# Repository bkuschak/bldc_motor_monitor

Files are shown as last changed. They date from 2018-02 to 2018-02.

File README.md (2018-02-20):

# bldc_motor_monitor
This is a tachometer, counter, and current meter for the LMS 5200 mini-lathe, LMS 3990 mini-mill and similar tools that use the XMT-DRV-500C(3) / ZM3404 BLDC motor controller.

This project provides a small 2x16 line LCD display showing:
- Spindle RPM and direction
- Spindle revolution counter
- Motor current

It consists of a small PCB hosting the LCD, Arduino Micro R3, and connectors that mate inline with the BLDC sensor cable. It uses an 
optional toroidal transformer to sense AC line current.  A single pushbutton is used to clear the rev count and alternate between
modes.

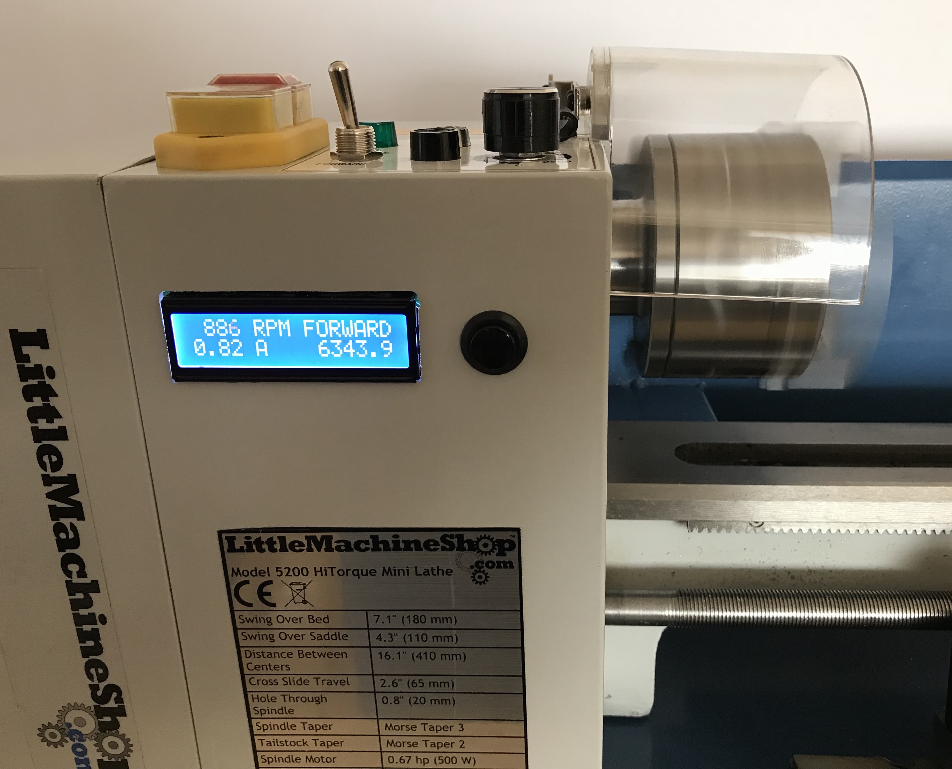
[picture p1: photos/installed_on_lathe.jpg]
Installed


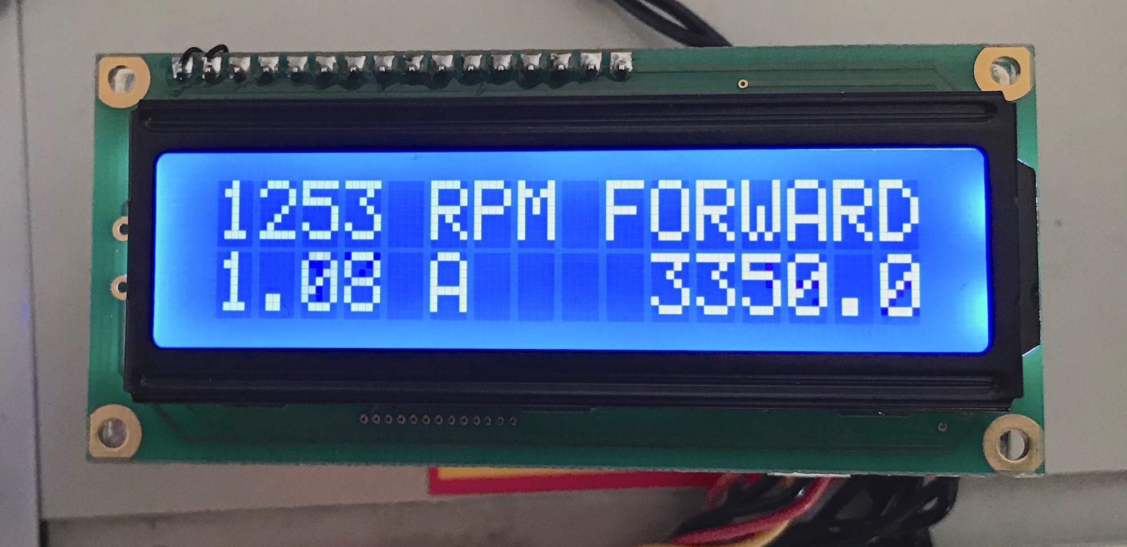
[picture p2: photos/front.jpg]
Front


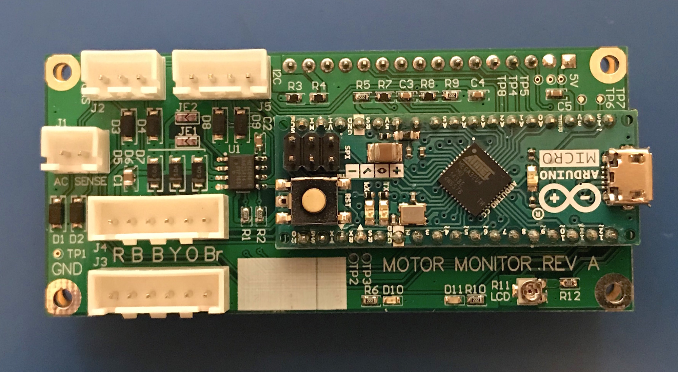
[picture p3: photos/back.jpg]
Back


This project was motivated by the need to keep an accurate count of spindle revolutions while winding coils on a mini-lathe. 
Since the BLDC motor controller already has a means of tracking spindle revolutions, it was easy to tap into this circuit rather than 
adding external encoders or hall-effect sensors.  

The motor controller in my lathe is this one pictured below. I haven't been able to find much good documentation on this board,
but it does seem to be pretty widely used. The pinout for the hall-effect connector is learned by inspection.  Recently I found 
a [very low-quality schematic](doc/500W-1000W_spindle_control_PCB_01.jpg?raw=true). It may or may not be for this particular driver board. 

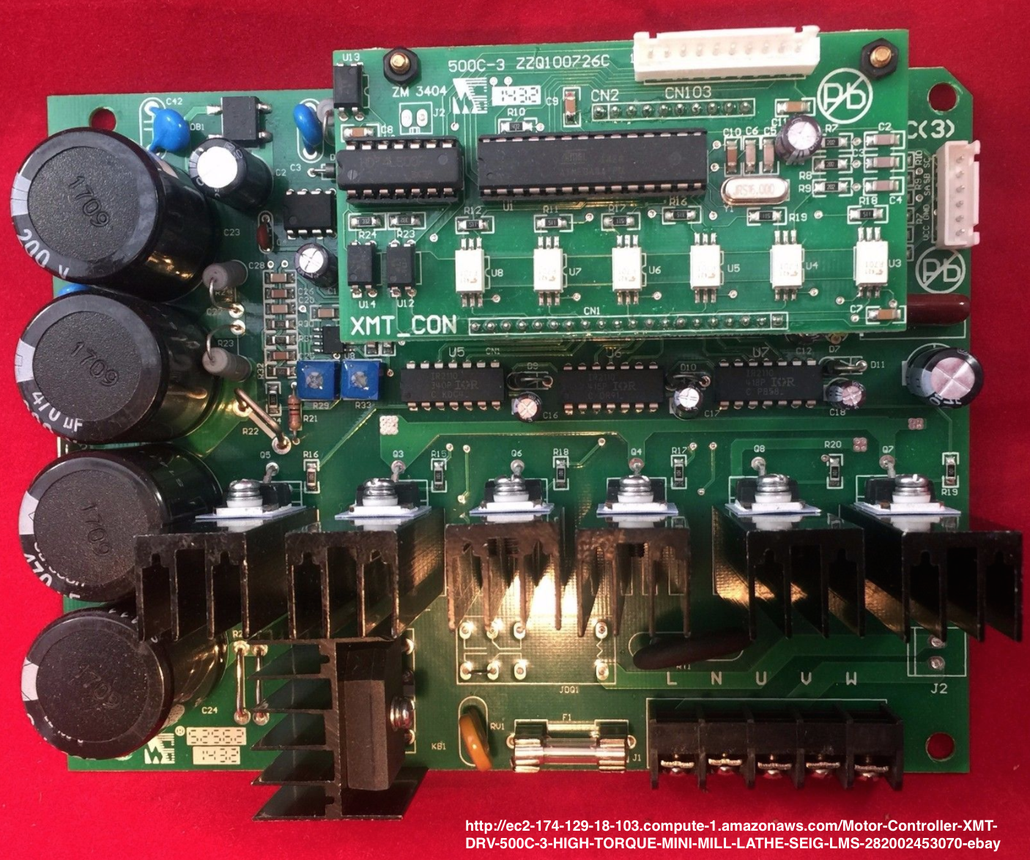
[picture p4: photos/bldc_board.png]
BLDC Board


### WARNING and DISCLAIMER
Although the BLDC 5V power seems to be isolated from AC mains and chassis, be careful to avoid 
risk of shock. I have no control over your BLDC driver circuitry, and it might zap you if you touch it. 
It is possible your machine uses a different driver board or a different hardware revision that is incompatible, even if it looks similar.
**Using this project can result in damage to your equipment, and danger or injury to yourself. If you choose to use 
this project, I will not be held liable for any damage or injury or repairs.**  Take all the usual precautions when working 
with AC-mains powered equipment. To avoid risk of damage to your PC, do not connect to the Arduino USB while the board is connected 
to the motor controller.

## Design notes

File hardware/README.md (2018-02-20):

## hardware

The schematics and PCB were created in Altium 16.

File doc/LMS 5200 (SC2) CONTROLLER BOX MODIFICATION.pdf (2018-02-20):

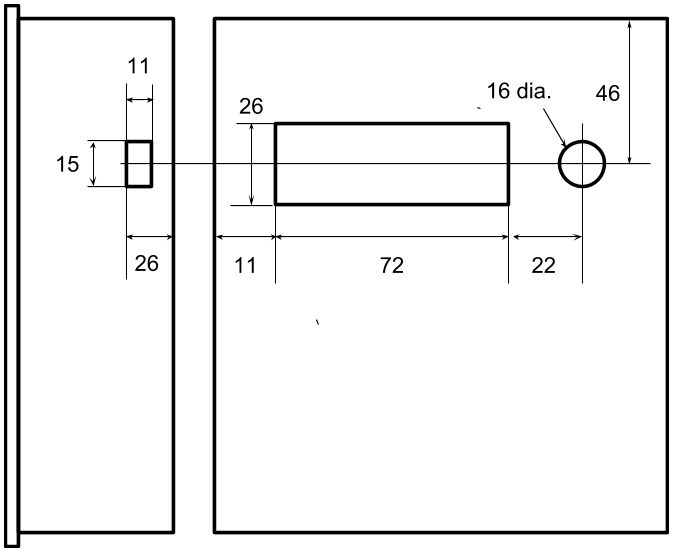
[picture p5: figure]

Dimensions in mm

LMS 5200 (SC2) CONTROLLER BOX MODIFICATION

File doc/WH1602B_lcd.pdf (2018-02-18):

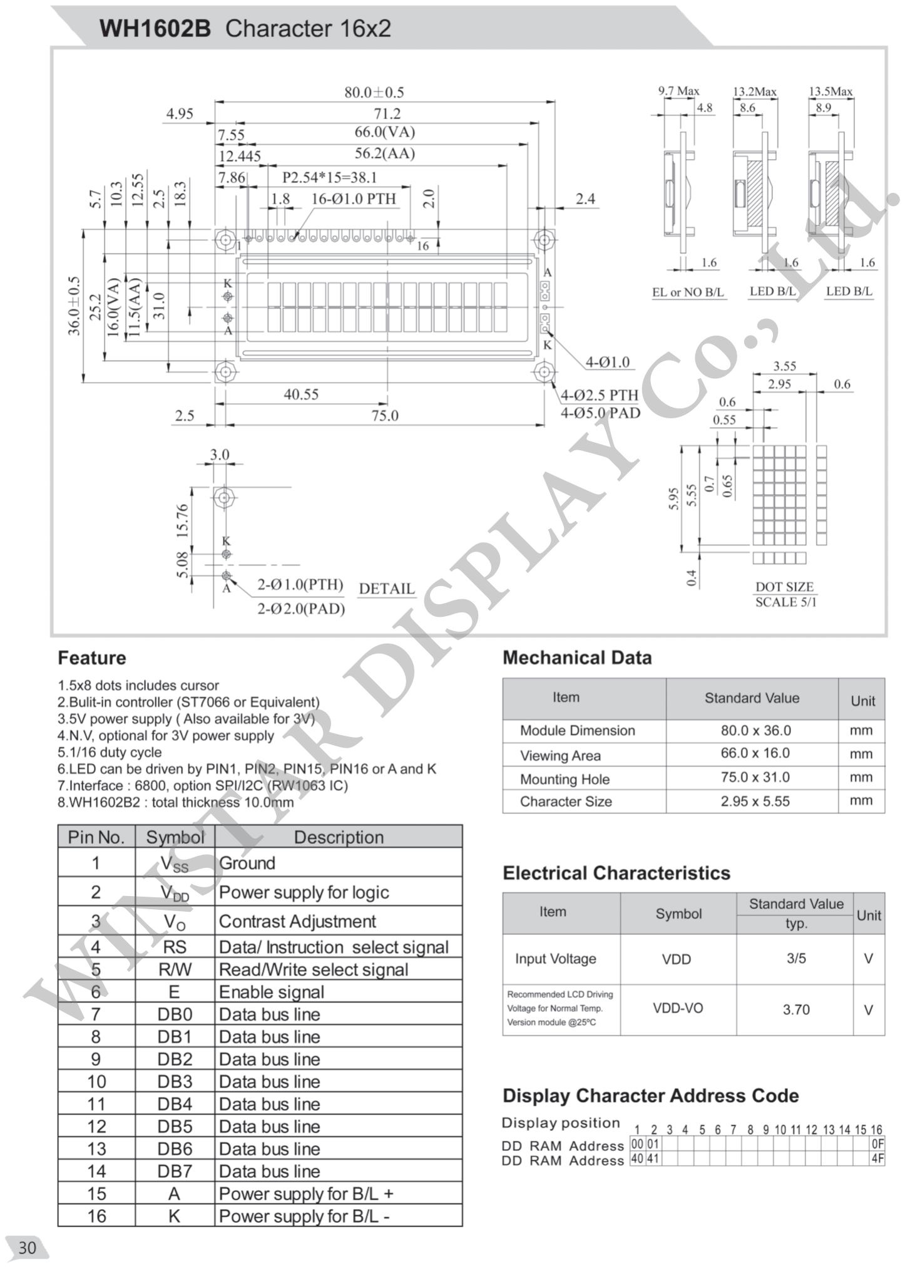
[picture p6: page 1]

WINSTAR DISPLAY Co., Ltd.

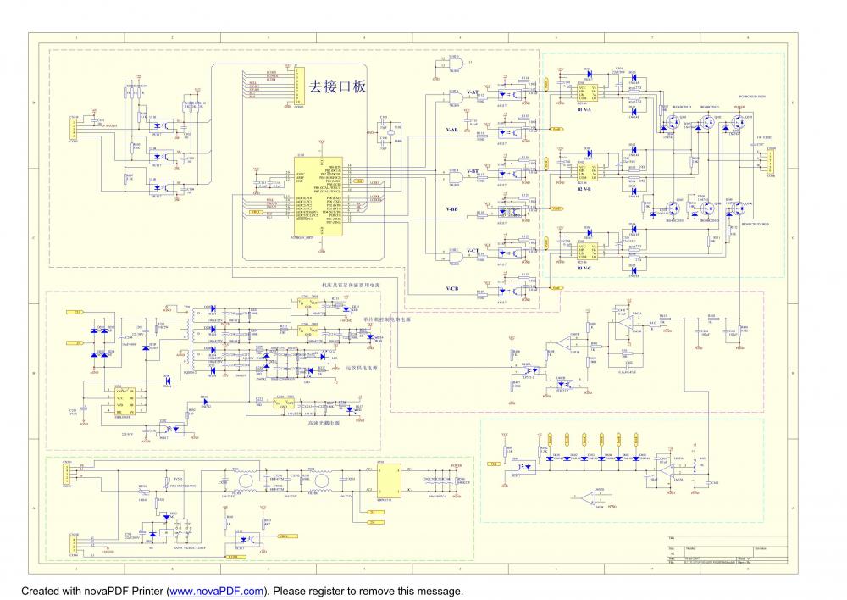
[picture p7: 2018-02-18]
doc/500W-1000W_spindle_control_PCB_01.jpg

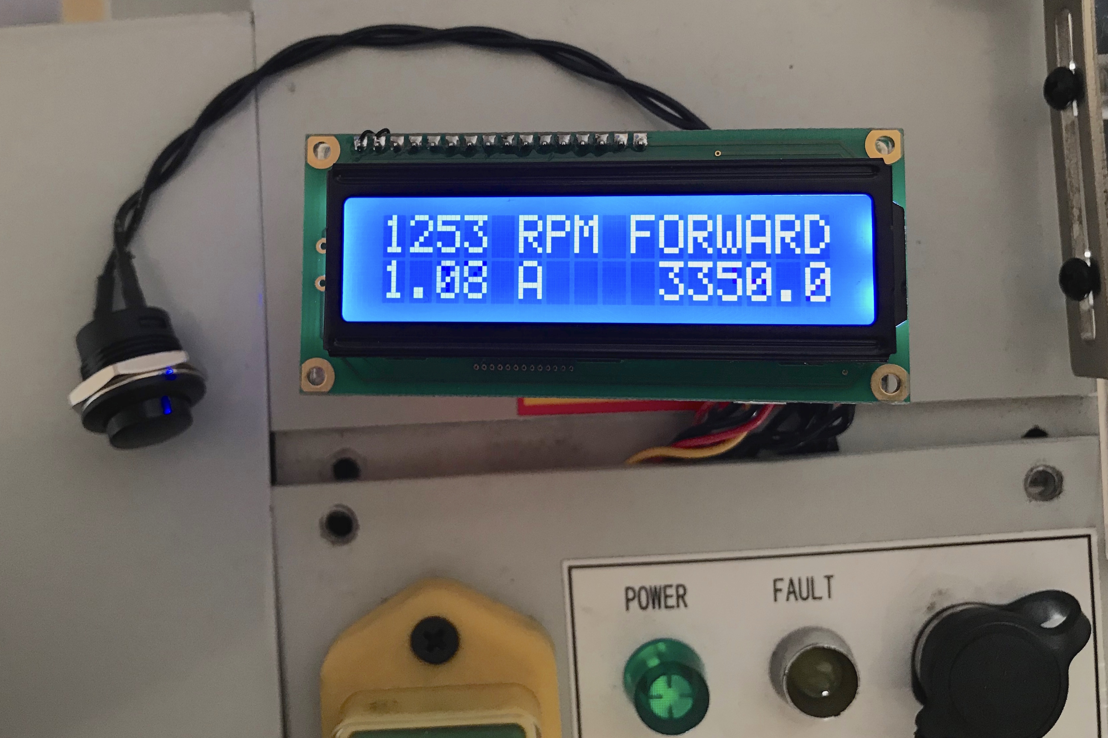
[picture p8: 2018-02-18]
photos/motor_monitor_pcb.jpg

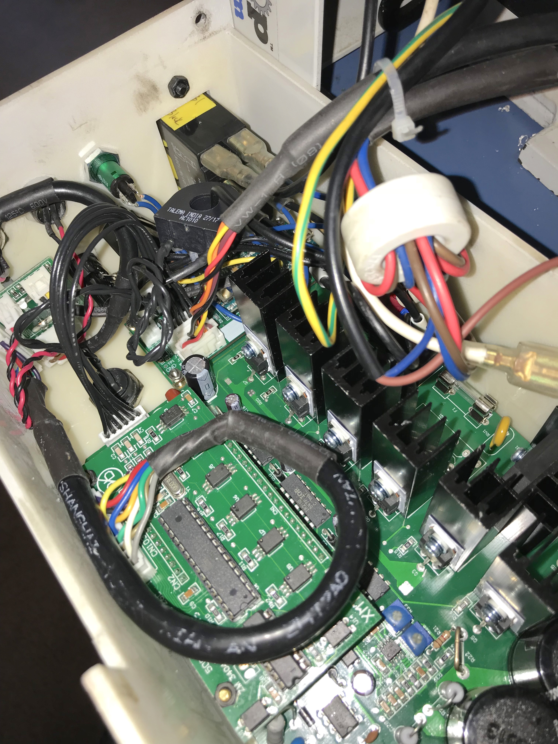
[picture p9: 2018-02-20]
photos/motor_controller_box_lathe2.jpg

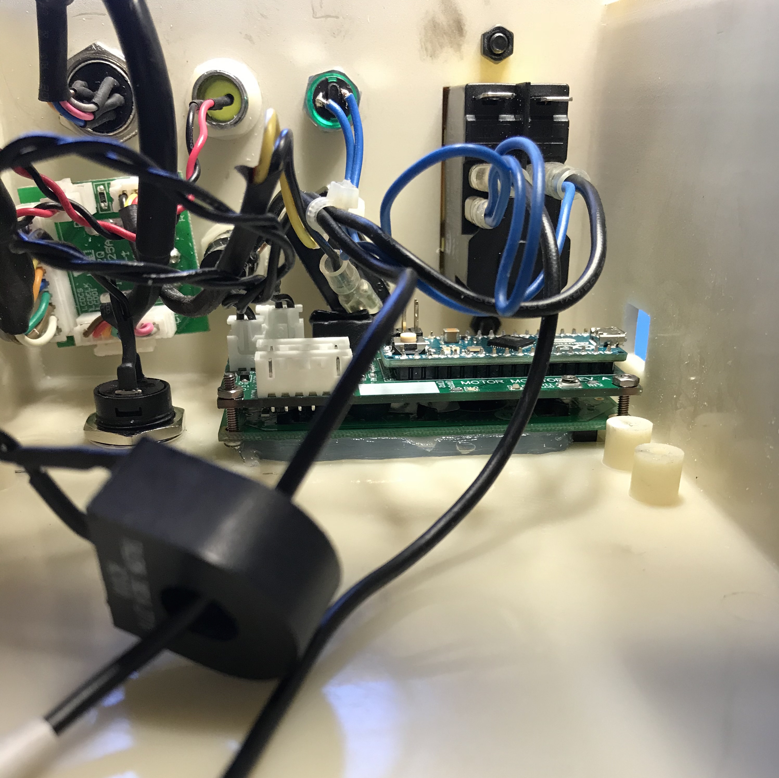
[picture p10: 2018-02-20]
photos/motor_controller_box_lathe1.jpg

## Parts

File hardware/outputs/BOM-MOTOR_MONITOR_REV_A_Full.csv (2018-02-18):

Quantity | DNS | Designator | Description | Footprint | Manufacturer | PartNumber | Digikey | Notes
1 |  | C1 | CAP CER 10UF 10V X7R 0805 | CAP 0805/2012 | Murata Electronics North America | GRM21BR71A106KE51L
4 |  | C2, C3, C4, C5 | CAP CER 0.1UF 16V X7R 0603 | CAP 0603/1608 | Murata Electronics North America | GRM188R71C104KA01D
9 |  | D1, D2, D3, D4, D5, D6, D7, D8, D9 | TVS DIODE 5VWM 9.2VC SOD123 | SOD123F | Littelfuse Inc. | SMF5.0A
1 |  | D10 | Typical RED, GREEN, YELLOW, AMBER GaAs LED | 0603R-GENERIC | Lite-On | LTST-C194KGKT
1 |  | D11 | Typical RED, GREEN, YELLOW, AMBER GaAs LED | 0603R-GENERIC | Osram | LS Q976-NR-1
1 |  | J1 | CONN HEADER XH TOP 2POS 2.5MM | JST XH B2B-XH-A | JST Sales America Inc. | B2B-XH-A(LF)(SN)
1 |  | J2 | CONN HEADER XH TOP 3POS 2.5MM | JST XH B3B-XH-A | JST Sales America Inc. | B3B-XH-A(LF)(SN)
2 |  | J3, J4 | CONN HEADER XH TOP 6POS 2.5MM | JST XH B6B-XH-A | DONGGUAN XINPEI PLASTIC HARDWARE ELECTRONIC CO LTD. | A2501WVB-06P |  | Preferred connector
2 | DNS | J3, J4 | CONN HEADER XH TOP 6POS 2.5MM | JST XH B6B-XH-A | JST Sales America Inc. | B6B-XH-A(LF)(SN) |  | Non latching substitute
1 |  | J5 | CONN HEADER XH TOP 4POS 2.5MM | JST XH B4B-XH-A | JST Sales America Inc. | B4B-XH-A(LF)(SN)
7 |  | R1, R2, R5, R6, R9, R10, R12 | RES SMD 2.2K OHM 5% 1/10W 0603 | RES 0603/1608 | Panasonic Electronic Components | ERJ-3GEYJ222V
4 |  | R3, R4, R7, R8 | RES SMD 51 OHM 5% 1/4W 0603 | RES 0603/1608 | Panasonic Electronic Components | ERJ-PA3J510V
1 |  | R11 | TRIMMER 2K OHM 0.15W SMD | POT Panasonic EVM | Panasonic Electronic Components | EVM-3YSX50B23
1 |  | U1 | FM24C04B FRAM | SO8_N | Cypress | FM24C04B-G | 428-3190-ND
1 | DNS | U2 | Arduino Micro R3 | ARDUINO_MICRO_R3 | Arduino | Micro R3
1 | DNS | U3 | 2x16 LCD STN Blue Negative |  | Winstar | WH1602B-TMI-JT
External components:
12 |  |  | Tin-plated terminals |  | DONGGUAN XINPEI PLASTIC HARDWARE ELECTRONIC CO LTD. | A2501-TBE |  | Preferred connector
1 |  |  | CONN HOUSING 2.5MM XH 6POS, LATCHING |  | DONGGUAN XINPEI PLASTIC HARDWARE ELECTRONIC CO LTD. | A2501HB-06P |  | Preferred connector terminals
1 | DNS |  | CONN HOUSING 2.5MM XH 6POS |  | JST Sales America Inc. | XHP-6 | 455-2218-ND | Non-latching substitute
1 |  |  | CONN HOUSING 2.5MM XH 3POS |  | JST Sales America Inc. | XHP-3 | 455-2219-ND
1 |  |  | CONN HOUSING 2.5MM XH 2POS |  | JST Sales America Inc. | XHP-2 | 455-2266-ND
11 |  |  | Jumper wire 6 inch |  | JST Sales America Inc. | ASXHSXH22K152 | 455-3240-ND
1 |  |  | SWITCH PUSH SPST-NO 6A 125V |  | CW Industries | GPB507A05BB | SW636-ND
1 |  |  | CURR SENSE XFMR 10A T/H |  | Talema Group | AC1010 | 1295-1102-ND
3 |  |  | Rubber bumbers |  | 3M | SJ-5003 (BLACK) | SJ5003-0-ND

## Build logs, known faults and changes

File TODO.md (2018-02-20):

## TODO

Several improvements should be made on the next rev:
- Fix swapped pins 1,2 on the LCD panel.
- DNS the I2C header, since it interferes with the forward/reverse switch.
- Add a DIP switch setting for forward/reverse sense, since lathe and mill use different direction for 'forward'.
- Add an output header to provide an (open-collector?) rotation and index pulses for use with a CNC controller.
- Avoid FRAM data corruption.
- Consider alternative OLED display with faster response.

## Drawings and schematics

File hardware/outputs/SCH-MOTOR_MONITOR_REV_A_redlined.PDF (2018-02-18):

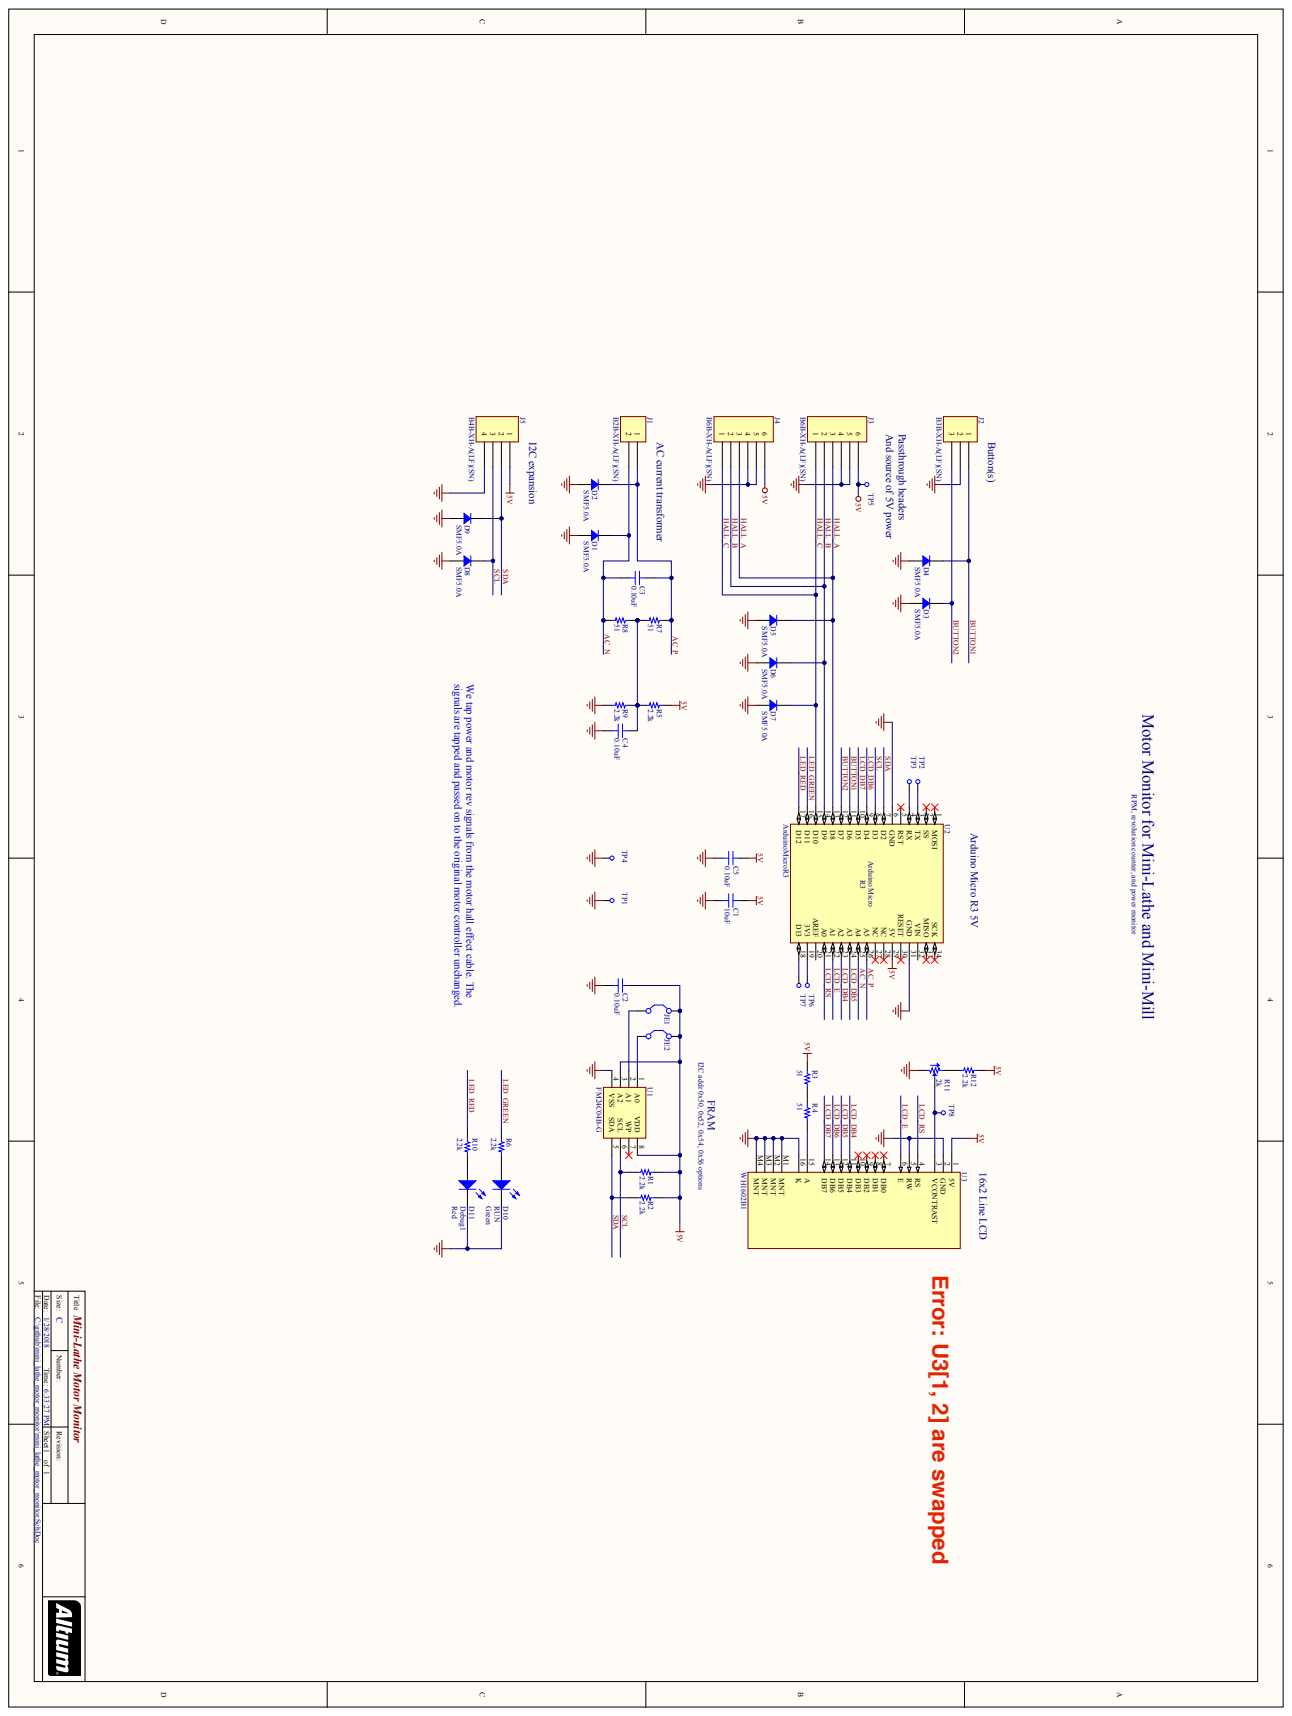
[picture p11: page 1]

And source of 5V power

signals are tapped and passed on to the original motor controller unchanged.

We tap power and motor rev signals from the motor hall effect cable. The

Motor Monitor for Mini-Lathe and Mini-Mill

RPM, revolution counter, and power monitor

D12 17 D13 18 3V3 19 AREF 20 A0 21 A1 22 A2 23 A3 24 A4 25 A5 26 NC 27 NC 28 5V 29 RESET 30 GND 31 VIN 32 MISO 33 SCK 34 Arduino Micro R3

VSS 4 SDA 5 SCL 6 WP 7 VDD 8

Mini-Lathe Motor Monitor

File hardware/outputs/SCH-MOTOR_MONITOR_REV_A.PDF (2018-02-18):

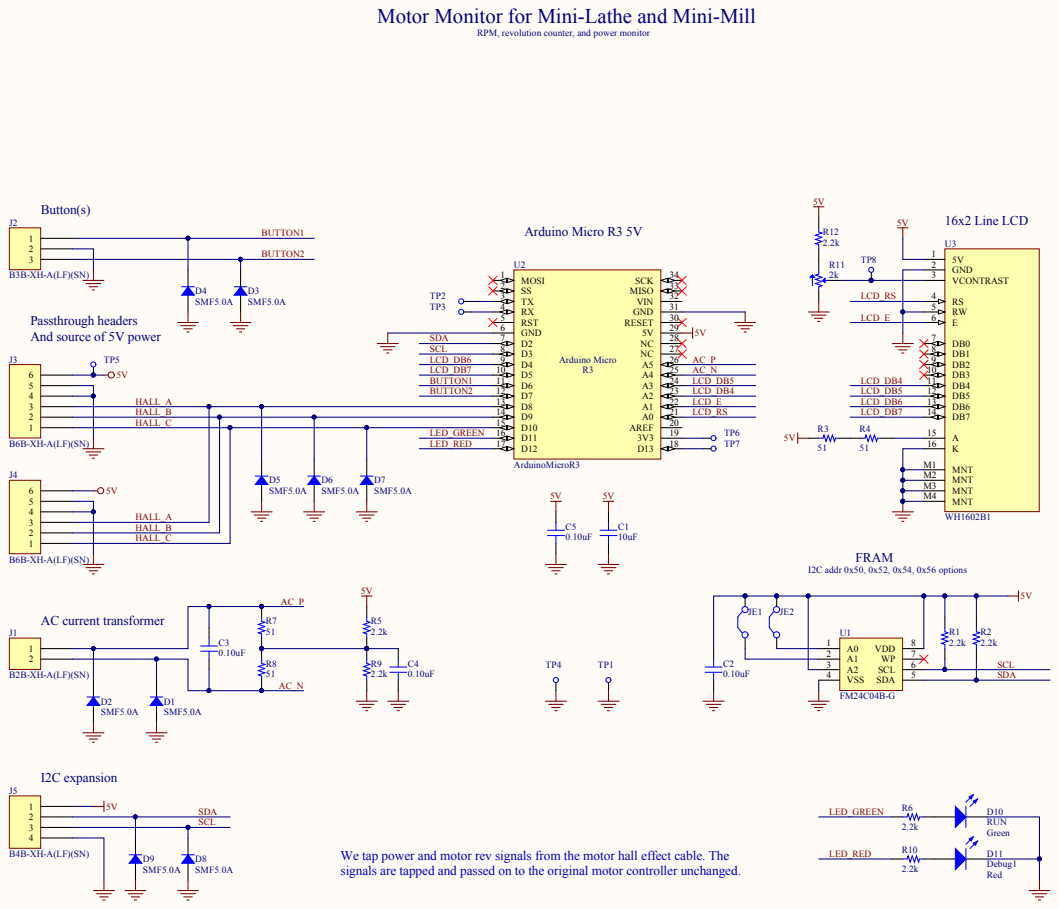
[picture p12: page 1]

Motor Monitor for Mini-Lathe and Mini-Mill

RPM, revolution counter, and power monitor

Passthrough headers
And source of 5V power

HALL_B | D9 14
HALL_C | | D10 15
5V | | | | D11 16

HALL_B
HALL_C

We tap power and motor rev signals from the motor hall effect cable. The
signals are tapped and passed on to the original motor controller unchanged.

Mini-Lathe Motor Monitor Title

Size: C | Number: | Revision:
Date: 1/28/2018 Time: 6:33:27 PM | | Sheet 1 of 1
File: C:\github\mini_lathe_motor_monitor\mini_lathe_motor_monitor.SchDoc

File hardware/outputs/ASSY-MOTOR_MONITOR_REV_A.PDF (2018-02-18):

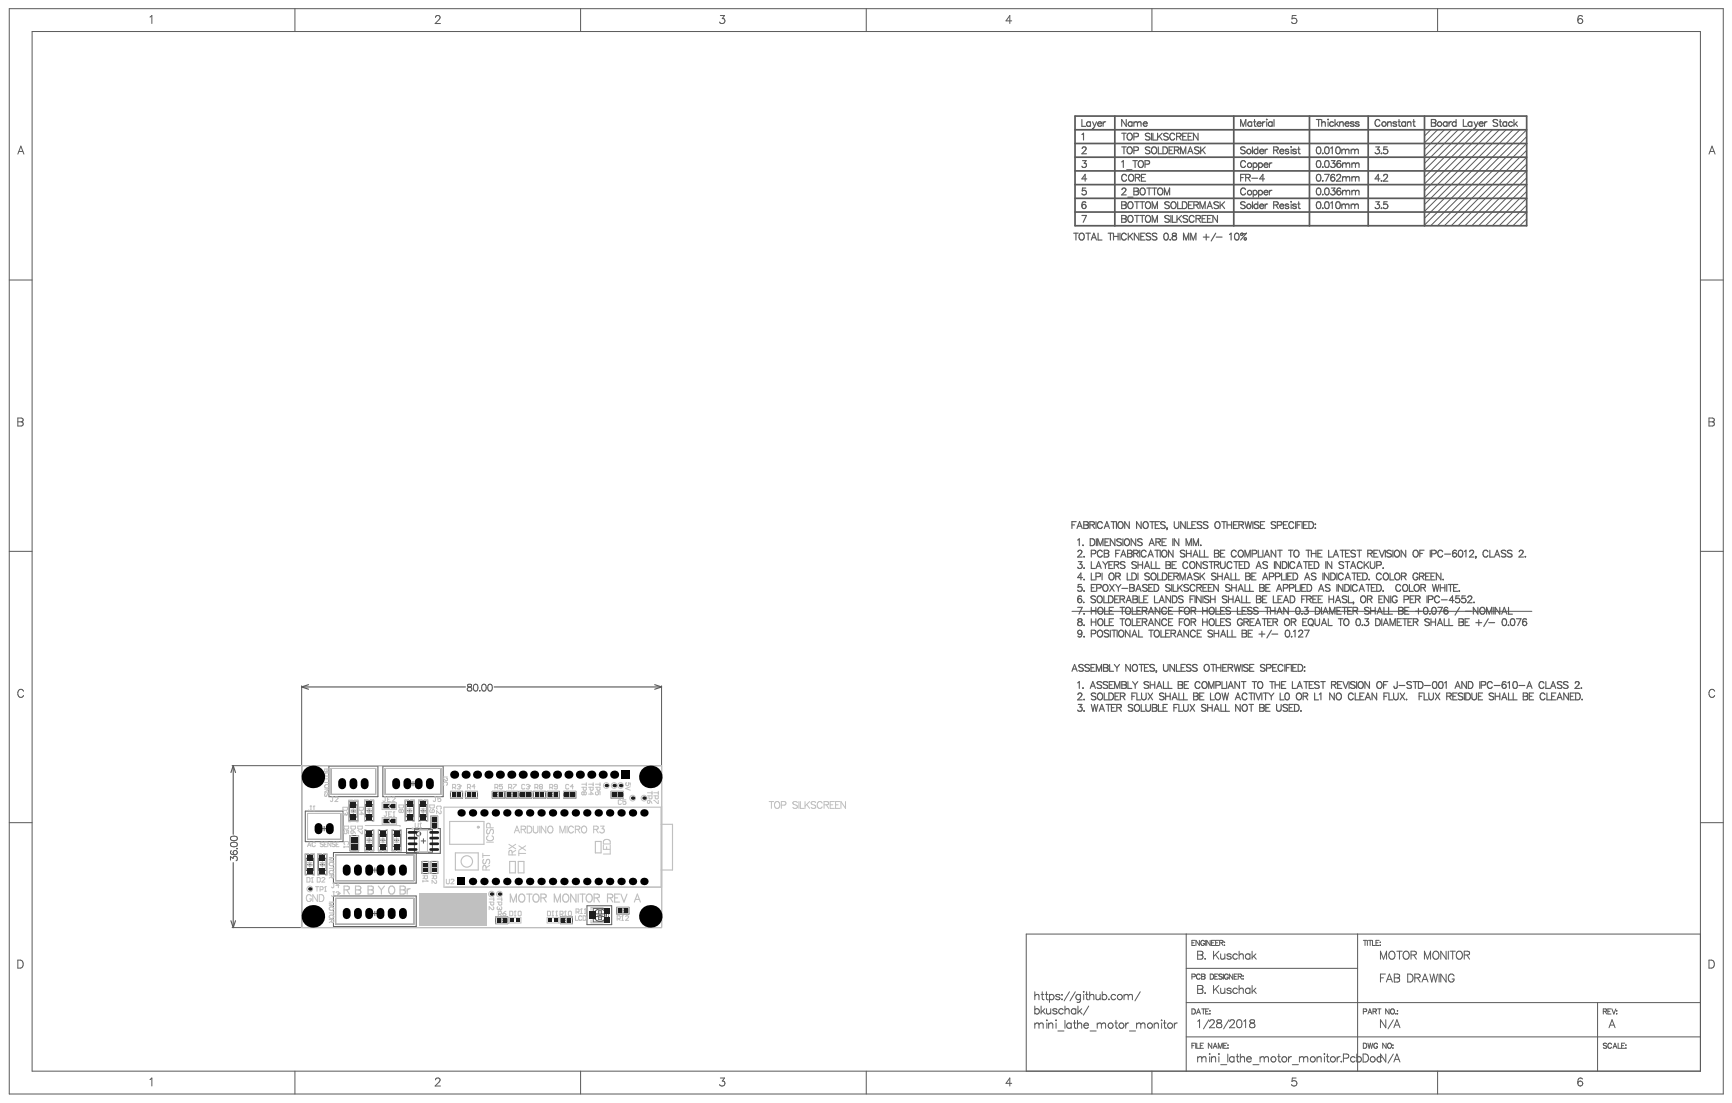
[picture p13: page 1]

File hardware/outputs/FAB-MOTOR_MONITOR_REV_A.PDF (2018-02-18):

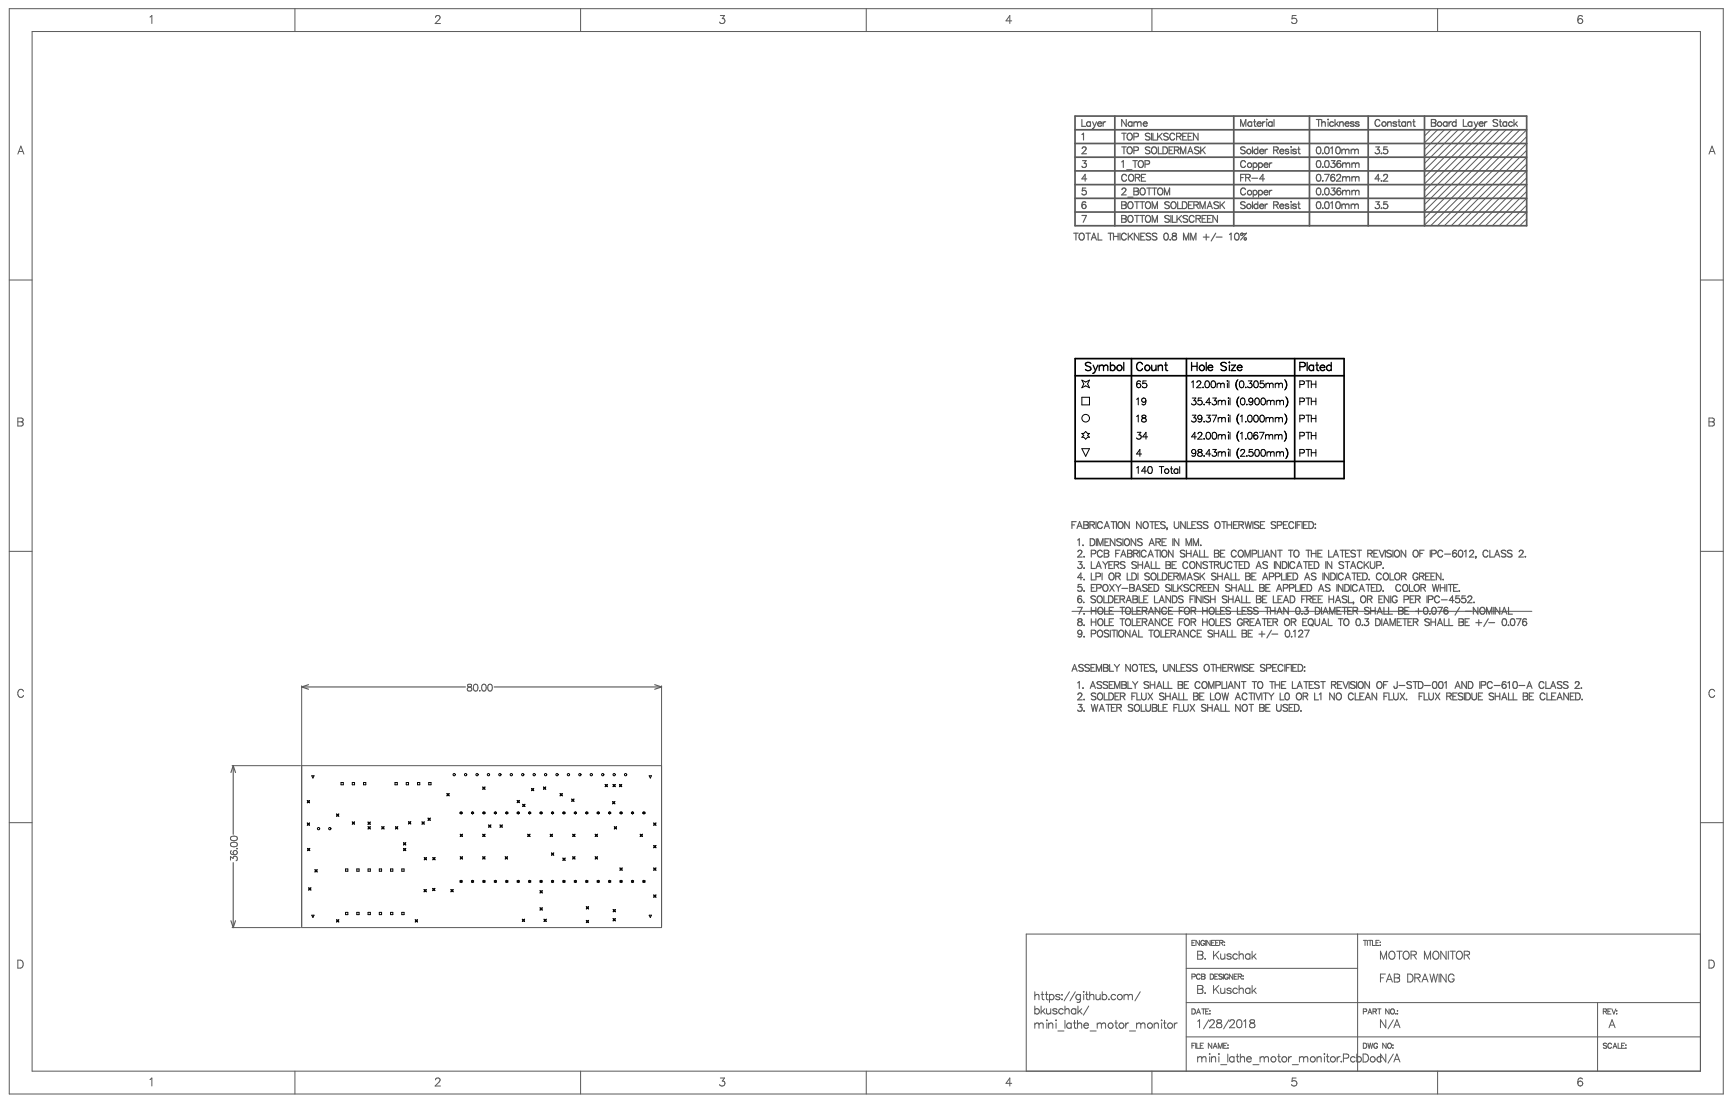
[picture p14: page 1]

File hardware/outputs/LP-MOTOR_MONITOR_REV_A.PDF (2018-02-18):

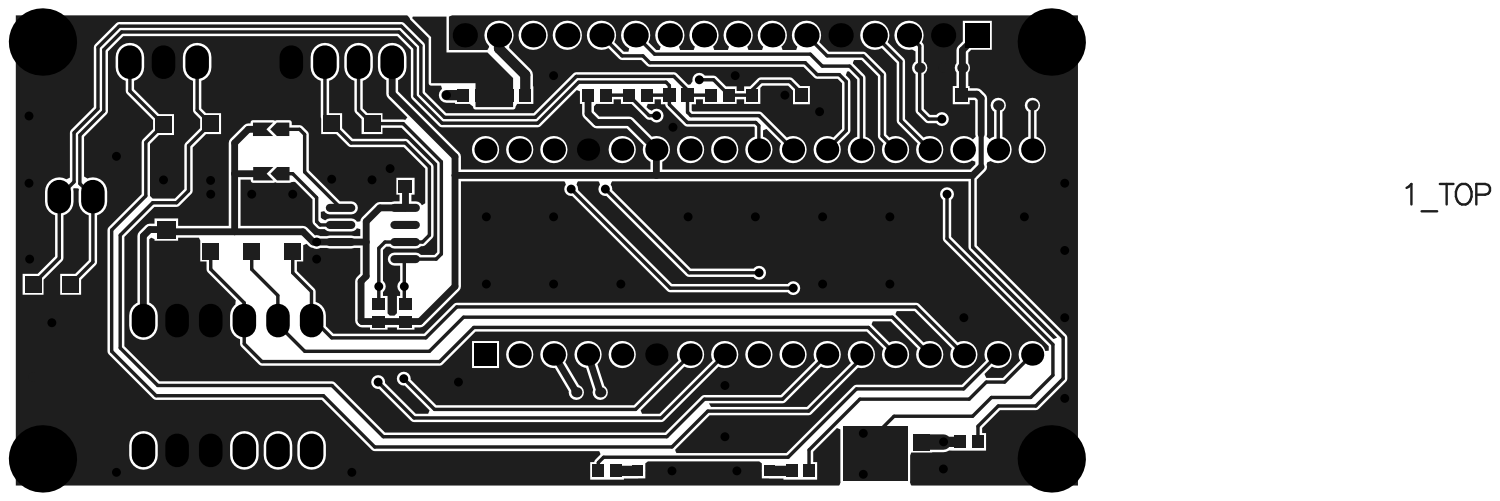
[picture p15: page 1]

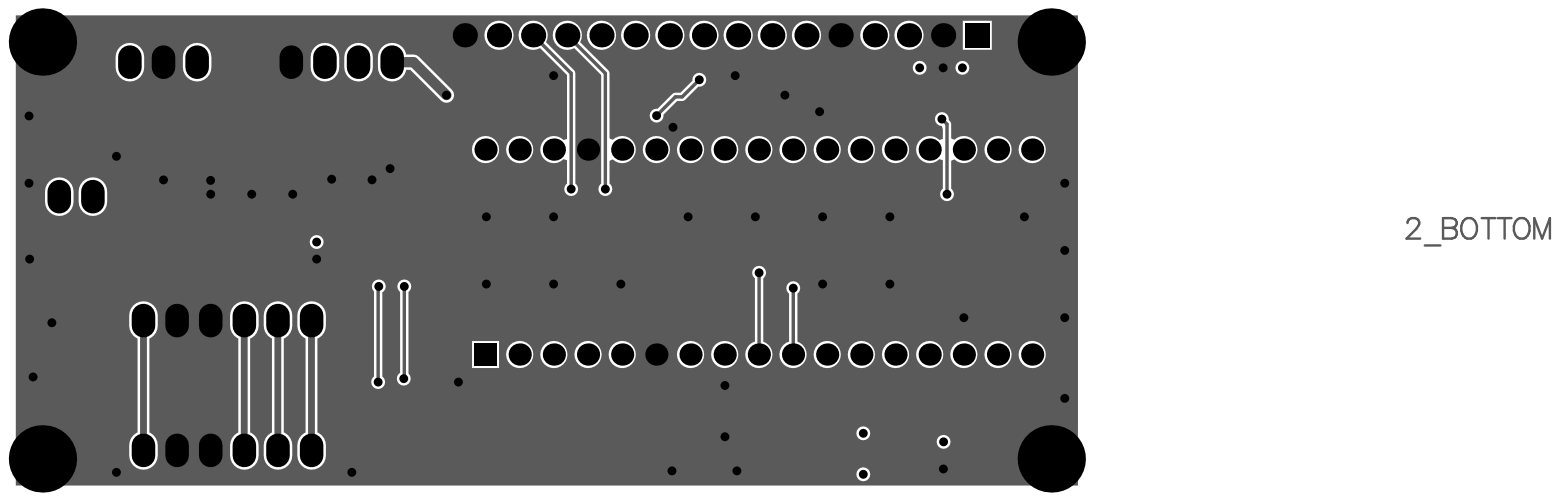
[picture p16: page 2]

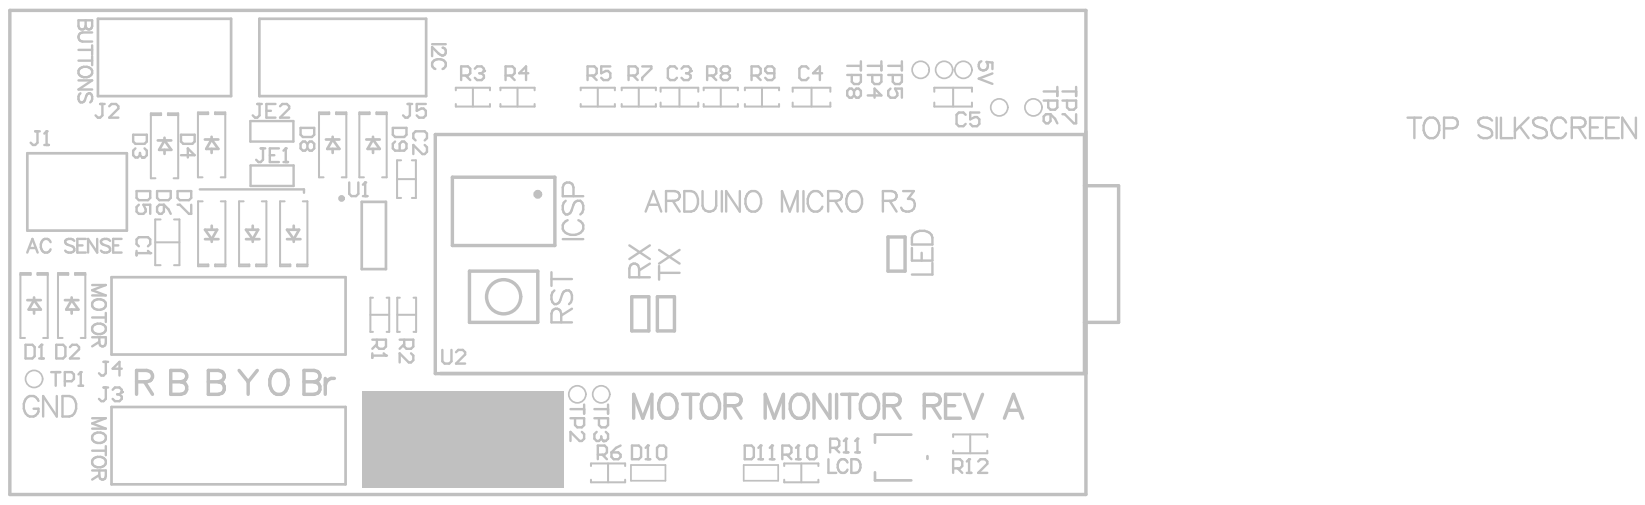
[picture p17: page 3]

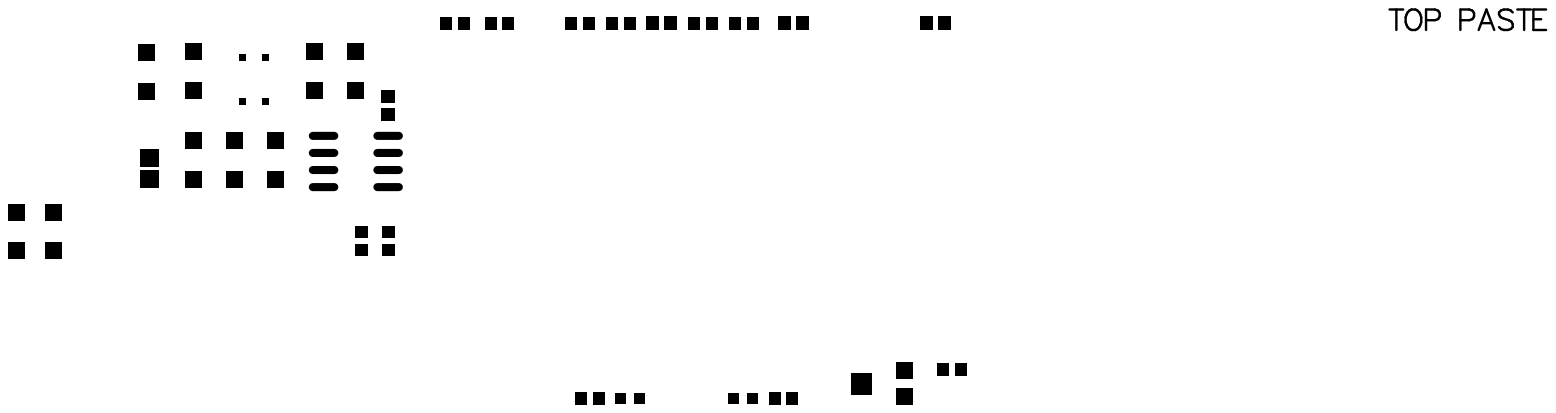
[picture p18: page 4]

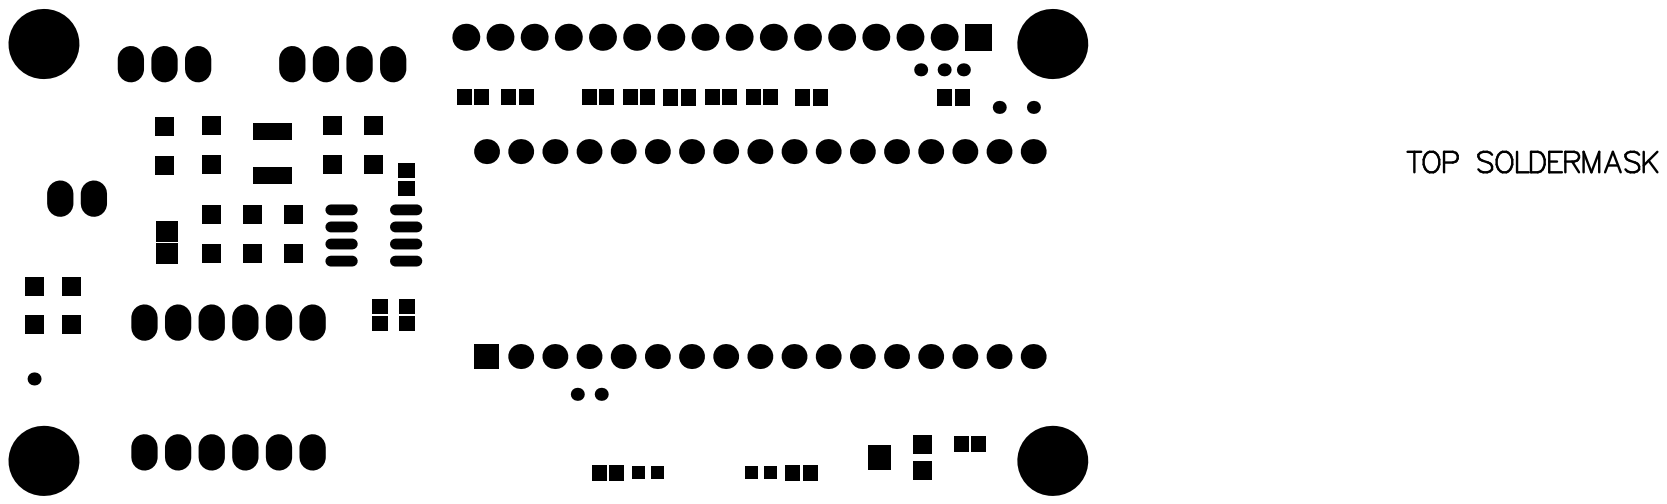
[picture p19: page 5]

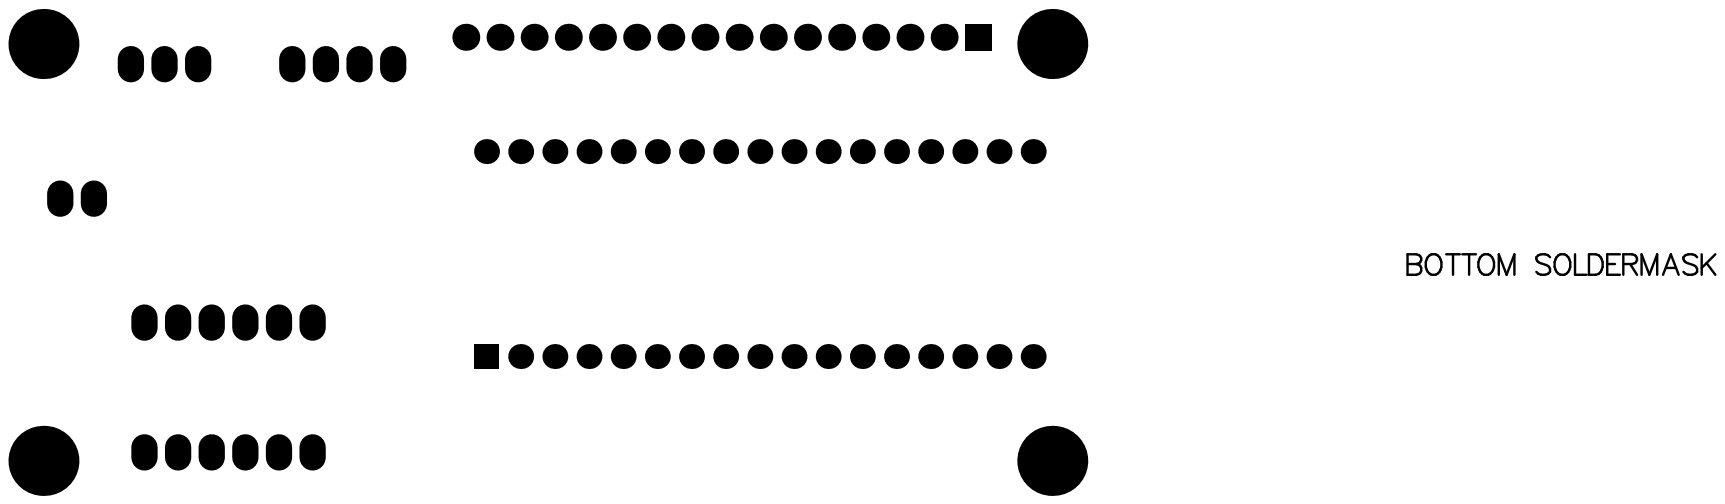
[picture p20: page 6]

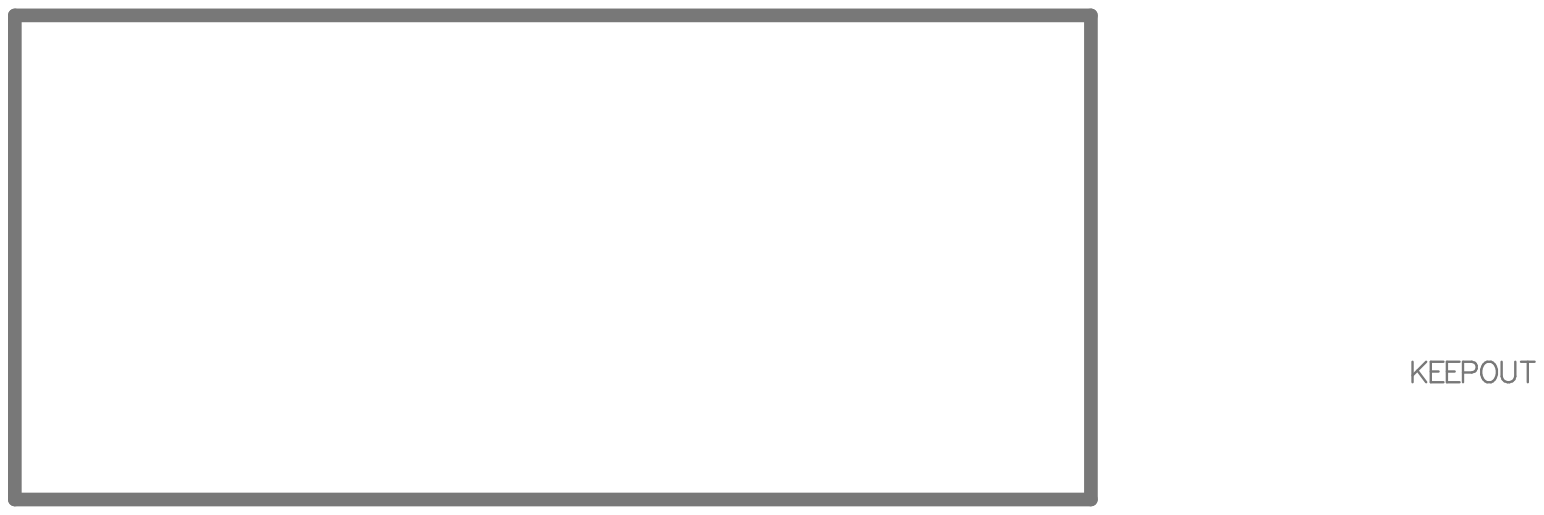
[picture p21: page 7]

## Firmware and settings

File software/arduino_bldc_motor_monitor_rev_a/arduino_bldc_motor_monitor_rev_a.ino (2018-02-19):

// Motor monitor for the LMS 5200 mini-lathe, LMS3990 mini-mill and similar
// tools that use the XMT-DRV-500C(3) / ZM3404 BLDC motor controller PCB.
//
// The monitor board plugs into the BLDC motor hall effect sensor connector,
// which supplies 5VDC power and position pulses. From this, and knowledge
// of the belt drive ratio, we calculate spindle speed and direction.
// We also keep a count of spindle revolutions, which is useful for coil winding.
//
// Rev count is periodically stored in an I2C FRAM so that a power interruption
// (which happens due to fault or safety activation) won't zero the count.
// We store two counts, total lifetime count (absolute) and incremental.
// Incremental count is erased by holding the pushbutton for a few seconds.
// Briefly pressing pushbutton switches between absolute and incremental mode.
//
// We also monitor the motor current using an isolated current sense transformer,
// and display the motor current on the LCD.
//
// Arduino Micro R3 - ATMEGA32U4 (Upload using the "Arduino Leonardo" setting)
// https://www.arduino.cc/en/uploads/Main/arduino-micro-schematic.pdf
// https://www.tonylabs.com/wp-content/uploads/arduino-micro-pinout-diagram.png
//
// Warning: Disconnnect the board from the BLDC motor controller when connecting
// to USB for programming!  Otherwise you risk damage to your motor driver and
// computer.
//
////////////////////////////////////////////////////////////////////////////////////////////
//
// Copyright 2017 B. Kuschak <bkuschak@yahoo.com>
//
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

#include <LiquidCrystal.h>
#include <Wire.h>

#include <avr/boot.h>

/////////////////////////////////////////////////////////////////////////
// These might be different based on your motor and drivetrain:
// Hall effect sensor
#define COUNTS_PER_MOTOR_REV  12            // hall counts per motor rev

// Drive belt ratio
#define DRIVE_RATIO           2.0           // motor revs per spindle rev

// Should be +1 or -1 depending on what constitutes 'forward' and 'reverse'
#define ROTATION_CONVENTION   -1
/////////////////////////////////////////////////////////////////////////

#define VER_STR               "Motor Mon v1.0.2"  // should be 16 characters
#define LCD_UPDATE_TIME_MSEC  850

// 3 Hall effect sensor inputs - on PCINT capable pins
#define PIN_HALL_A            8             // PB4 (board pin 8)
#define PIN_HALL_B            9             // PB5 (board pin 9)
#define PIN_HALL_C            10            // PB6 (board pin 10)

// LCD
#define PIN_LCD_RS            A0            // PF7 (board pin A0)
#define PIN_LCD_EN            A1            // PF6 (board pin A1)
#define PIN_LCD_D4            A2            // PF5 (board pin A2)
#define PIN_LCD_D5            A3            // PF4 (board pin A3)
#define PIN_LCD_D6            4             // PF3 (board pin 
#define PIN_LCD_D7            5             // PF2 (board pin 

// Differential ADC
#define PIN_CURR_SENSE_N      A4            // Analog input (ADC1)
#define PIN_CURR_SENSE_P      A5            // Analog input (ADC0)

#define LED_RED               12
#define LED_GREEN             11
#define BUTTON_1              6             // D6 (board pin 11)
#define BUTTON_2              7             // D7 (board pin 12)

// FRAM to store our recent rev count
#define FRAM_I2C_ADDR         0x54          // FIXME - schematic error on A2, A0
#define FRAM_SIGNATURE        0xACDC1234
#define FRAM_VERSION          1

#define DISPLAY_INCREMENTAL   0
#define DISPLAY_LIFETIME      1

LiquidCrystal lcd(PIN_LCD_RS, PIN_LCD_EN, PIN_LCD_D4, PIN_LCD_D5, PIN_LCD_D6, PIN_LCD_D7);

volatile int32_t hall_count;
volatile uint16_t incr_abs_hall_count;
volatile uint32_t hall_count_time;
volatile uint32_t errors;
volatile int8_t last_hall_seq;
volatile uint32_t adc_overflows;
volatile uint32_t adc_count;
volatile int16_t adc_val;
volatile int32_t adc_rms;
volatile bool adc_flag;
volatile int16_t adc_sum, adc_filter;
int8_t dir;
uint8_t power_pct;
uint32_t adc_sample_rate;
float rpm;
float motor_curr;
uint8_t rev_display_mode;
int32_t rpm_update_hall_count;
uint32_t rpm_update_time;

// Note, Wire library has a limitation of <32 bytes, so this has to be smaller
struct fram_data_t
{
  uint32_t signature;
  uint32_t version;
  int64_t  lifetime_hall_count;
  int32_t  hall_count;
  uint32_t reserved1;
  uint32_t csum;
} __attribute__((aligned(8), packed)) fram_data;


// Store rev count in FRAM.  FRAM lifetime is essentially unlimited, however power loss
// during read or write can corrupt the value.  So store it in two checksummed blocks.
// At least one should survive.

int store_fram(void)
{
  uint8_t addr;
  uint8_t *ptr8;
  uint32_t *ptr32;
  uint8_t i, j;
  uint32_t csum = 0;
  uint8_t fram_addr = 0;

  fram_data.signature = FRAM_SIGNATURE;
  fram_data.version = FRAM_VERSION;
  fram_data.reserved1 = 0;
  fram_data.hall_count = hall_count;

  // Accumulate recent to lifetime total
  noInterrupts();
  fram_data.lifetime_hall_count += incr_abs_hall_count;
  incr_abs_hall_count = 0;
  interrupts();

  // compute checksum
  fram_data.csum = 0;
  csum = 0;
  ptr32 = (uint32_t*)&fram_data;
  for (i = 0; i < sizeof(fram_data) / sizeof(uint32_t); i++)
    csum += *ptr32++;
  fram_data.csum = ~csum;                       // so all zero doesn't fool us

  // write 2 copies of data to I2C FRAM.  if power fails during write, the other one should
  // remain intact.  FIXME - this assumes power fails quickly.  
  for (j = 0; j < 2; j++) {

    // We use 4Kbit FRAM: it has 8 bit address plus one page select bit
    Wire.beginTransmission(FRAM_I2C_ADDR);      // slave write, page zero
    Wire.write(fram_addr);                      // addr
    ptr8 = (uint8_t*)&fram_data;
    for (i = 0; i < sizeof(fram_data); i++)
      Wire.write(*ptr8++);
    Wire.endTransmission();

    // FIXME Verify write was successful before starting next? (in case power is going down 
    // while we're writing.) Complicated because FRAM read is destructive at the physical level.
    // So a verify may succeed, but actually the data can't be immediately rewritten.

    fram_addr += sizeof(fram_data);
  }
}

// There should be two identical copies of data in the FRAM.  Read and select the first one that
// has a valid checksum.

int load_fram(void)
{
  uint8_t addr;
  uint8_t *ptr8;
  uint8_t i, j;
  uint32_t *ptr32;
  uint32_t csum;
  uint8_t fram_addr = 0;

  for (j = 0; j < 2; j++) {
    ptr8 = (uint8_t*)&fram_data;

    // read I2C FRAM
    // We use 4Kbit FRAM: it has 8 bit address plus one page select bit
    Wire.beginTransmission(FRAM_I2C_ADDR);                  // slave write, page zero
    Wire.write(fram_addr);                                  // addr
    Wire.endTransmission();                                 // Does issue stop
    Wire.requestFrom(FRAM_I2C_ADDR, sizeof(fram_data));
    for (i = 0; i < sizeof(fram_data) && Wire.available(); i++)
      *ptr8++ = Wire.read();

    // validate checksum
    csum = 0;
    ptr32 = (uint32_t*)&fram_data;
    for (i = 0; i < sizeof(fram_data) / sizeof(uint32_t); i++)
      csum += *ptr32++;
    csum += 1;
    if (csum == 0) {
      // Make sure it's one we recognize
      if (fram_data.signature == FRAM_SIGNATURE) {
        switch (fram_data.version) {
          case FRAM_VERSION:
            // this is our native version
            hall_count = fram_data.hall_count;
            rpm_update_hall_count = hall_count;   // to avoid glitch on first RPM calc
            return 0;                             // use it
          // In future releases we might need to do some translation here..
          //case FRAM_VERSION-1:
          // translate as needed...
          default:
            // unrecognized version - ignore it.
            ;
        }
      }
    }
    fram_addr += sizeof(fram_data);
  }

  // No valid checksum found.  store a good one.  If this happens during
  // normal operation, we will lose the lifetime rev count...  Maybe we should store that differently?
  store_fram();
  return -1;
}

// Return hall sensors value as a 3 bit number
uint8_t get_hall_sensors(void)
{
  uint8_t idx;

  // FIXME - do this with port I/O as it is slow using digitalRead()
  idx = digitalRead(PIN_HALL_A) << 2 | digitalRead(PIN_HALL_B) << 1 | digitalRead(PIN_HALL_C);
  idx &= 0x7;
  return idx;
}

// interrupt on change for the hall effect sensor pins
void hall_handler(void)
{
  // hall sensors form a three bit code with 6 valid values.
  // see http://hades.mech.northwestern.edu/index.php/Brushless_DC_Motors
  // table index = hall_sensors[A,B,C]. illegal states are -1
  // two table cycles equals one motor revolution.
  static const int8_t hall_seq_table[] = { -1, 4, 2, 3, 0, 5, 1, -1 };
  int8_t seq;
  int8_t diff;

  // timestamp the pulse for more accurate RPM calculation
  hall_count_time = micros();

  seq = hall_seq_table[get_hall_sensors()];

  if (seq < 0)
    return;

  diff = seq - last_hall_seq;
  last_hall_seq = seq;

  // handle wraparound
  if (diff == -5)
    diff = 1;
  else if (diff == 5)
    diff = -1;

  // Lathe motor rotation sense is opposite (+1 count is reverse, -1 is forward)

  if (diff == (1 * ROTATION_CONVENTION)) {
    hall_count++;
    dir = 1;
    incr_abs_hall_count++;       // will accumulate this to the lifetime total in FRAM
  }
  else if (diff == (-1 * ROTATION_CONVENTION)) {
    hall_count--;
    dir = -1;
    incr_abs_hall_count++;
  }
  else {
    // we missed a count or the sensors are wired incorrectly
    errors++;
  }
}

float hall_count_to_revs(int32_t count)
{
  return (float)count / COUNTS_PER_MOTOR_REV / DRIVE_RATIO;
}

float get_revs()
{
  return hall_count_to_revs(hall_count);
}

// Pin change interrupt config
void pcintSetup(byte pin)
{
  *digitalPinToPCMSK(pin) |= bit (digitalPinToPCMSKbit(pin));  // enable pin
  PCIFR  |= bit (digitalPinToPCICRbit(pin)); // clear any outstanding interrupt
  PCICR  |= bit (digitalPinToPCICRbit(pin)); // enable interrupt for the group
}

// Interrupt service routine for pin change interrupt on D8 to D13
ISR (PCINT0_vect)
{
  hall_handler();
}

// Interrupt service routine for the ADC completion.
// This takes some time during calculation, we should verify we're not overruning.
ISR(ADC_vect)
{
  uint8_t decimation = 4;

  // Right-justified 2s complement
  // Must read low first
  adc_val = ADCL;
  adc_val |= (((uint16_t)ADCH) << 8);
  adc_val <<= 6;
  adc_val >>= 6;

  adc_sum += adc_val;

  // Decimate and then run the RMS calculator
  if ((adc_count % decimation) == 0) {
    // HPF to remove any ADC offset
    adc_filter = high_pass_filter(adc_sum);
    adc_filter /= decimation;

    // Run the recursive RMS calculation
    adc_rms = calc_rms(adc_filter);
    adc_sum = 0;
  }
  adc_count++;
}

// ADC ISR that samples AC current and computes RMS power (assuming a certain power factor)
// Interrupt driven ADC adapted from
// http://www.glennsweeney.com/tutorials/interrupt-driven-analog-conversion-with-an-atmega328p
//
// ADC sample rate is
//  differential mode: (Fcpu / 128) / 14 => (16e6 / 128) / 14 = 8929 Hz
//  single endeded mode: (Fcpu / 128) / 14 => (16e6 / 128) / 13 = 9616 Hz
//
// in Gain = 1, ADC max input is +/-2.56 V or 5.12 Vpp or 1.81 Vrms.
// in Gain = 10, ADC max input is +/-0.256 V or 0.512 Vpp or 181 mVrms.
// The actual range will be reduced by the ADC offset error, and limited by ~5V VCC.
//
// The RMS calculation is positive only, so its range is half of the ADC range.
// ADC peak is 512 DN, max RMS measureable without clipping is 361 DN, again limited by ADC offset.
//
// Our current transformer will ouput 0.1Vrms @ 1A and 1Vrms @ 10A (into 100 ohm),
// so use Gain=1 for >10 Arms full scale.
// RMS(A) = DN / 512 / Gain * 2.56 / 0.1
//
// Typically we're using a fraction of the 1X range, but 10X is too small.
// Maybe we can use variable gain?  If the sensed value isn't clipping then switch to 10X mode?
// With the decimation and RMS averaging, it seems to be good enough for now...

void init_adc(void)
{
  // Disable Digital inputs for ADC0 and ADC1
  DIDR0 |= 0x3;

  // Configure ADC for differential mode
  // Full scale +/- VREF/Gain
  ADMUX = 0xC0;             // internal 2.56V Vref
  //ADMUX = 0x40;             // AVCC Vref

  ADMUX |= 0x10;            // MUX[5:0] = 0x10: POS = ADC0, NEG = ADC1, GAIN = 1.
  //ADMUX |= 0x09;            // MUX[5:0] = 0x09: POS = ADC1, NEG = ADC0, GAIN = 10
  //ADMUX |= 0x00;            // MUX[5:0] = 0x00: POS = ADC0, NEG = GND, GAIN = 1
  //ADMUX |= 0x01;            // MUX[5:0] = 0x01: POS = ADC1, NEG = GND, GAIN = 1

  ADCSRA = 0xA7;            // Enable auto, prescaler=128
  ADCSRB = 0x00;            // MUX[5] = 0, free-running mode
  ADCSRA |= 0x08;           // enable interrupts

  adc_flag = false;
  ADCSRA |= 0x40;           // kick off the first conversion
}


// Recursive single pole high pass filter.
// Removes any ADC offset prior to computing the AC(rms) voltage.
//
// Fc = normalized corner frequency from 0 to 0.5 (0 to Fs/2).
// We set Fc = 4 Hz.  Fs = 8928.   Fc(normalized) = 8.96e-4
// x = e^(-2*pi*Fc_norm)
// a0 = (1+x)/2
// a1 = -(1+x)/2
// b1 = x
//
#define HPF_Fc_Hz     4.0
#define ADC_Fs        8928.0
#define HPF_Fc        (HPF_Fc_Hz/(ADC_Fs/2))
#define HPF_X(fc)     (exp(-2*3.14*fc))
#define HPF_A0(x)     ((1.0+x)/2)
#define HPF_A1(x)     (-(1.0+x)/2)
#define HPF_B1(x)     (x)

int32_t high_pass_filter(int16_t x)
{
  float a0 = HPF_A0(HPF_X(HPF_Fc));
  float a1 = HPF_A1(HPF_X(HPF_Fc));
  float b1 = HPF_B1(HPF_X(HPF_Fc));
  float y;
  static float xn_1, yn_1;

  y = a0 * x + a1 * xn_1 + b1 * yn_1;
  xn_1 = x;
  yn_1 = y;
  return y;
}

// Use a recursive low pass filter to calculate the root mean squared.
// FIXME - not enough horsepower to run this floating point calc at full ADC rate.
//
#define RMS_Fc_Hz     2.0
#define RMS_Fc        (RMS_Fc_Hz/(ADC_Fs/2))
#define RMS_X(fc)     (exp(-2*3.14*fc))
#define RMS_A0(x)     (1.0-x)
#define RMS_B1(x)     (x)

int32_t calc_rms(int16_t x)
{
  float b1 = RMS_B1(RMS_X(RMS_Fc));
  float a0 = RMS_A0(RMS_X(RMS_Fc));
  float y;
  float xsq = (float)x * x;
  static float yn_1;

  // LPF the square of the signal.  This is the mean of squares.
  y = a0 * xsq + b1 * yn_1;
  yn_1 = y;

  // return root of mean of squares
  return sqrt(y);
}

// 2x16 LCD
// 0123456789012345
// ----------------
// 1400 RPM FORWARD
// 1.23 A -999999.9
// ----------------
// 1500 RPM REVERSE
// 1.23 A 9999999.9
// ----------------

void update_lcd(void)
{
  char str_revs[12];
  char str_curr[6];
  char str[21];
  static uint32_t last_errors;
  static uint8_t last_mode;

  // Testing
  //motor_curr = 9.99;
  //rpm = 1234;
  //hall_count = 80000000.0 * COUNTS_PER_MOTOR_REV * DRIVE_RATIO;
  // seems like +/-89e6 is the limit (continuous operation for 24 days)

  // First line
  // 1400 RPM FORWARD
  snprintf(str, sizeof(str), "%4u RPM %s",
           abs((int)rpm),
           ((dir > 0) ? "FORWARD" :
            ((dir < 0) ? "REVERSE" : "FORWARD" )),
           str_curr);
  str[16] = 0;
  lcd.setCursor(0, 0);
  lcd.print(str);

  // Second line
  // 3.23 A -999999.9
  // FIXME handle wraparound
  dtostrf(motor_curr, 3, 2, str_curr);    // snprintf doesn't have %f
  if (rev_display_mode == DISPLAY_LIFETIME)
    //snprintf(str_revs, sizeof(str_revs), "%9lu",
    dtostrf(fram_data.lifetime_hall_count / COUNTS_PER_MOTOR_REV / DRIVE_RATIO, 9, 0, str_revs);
  else
    dtostrf(get_revs(), 9, 1, str_revs);    // snprintf doesn't have %f
  str_curr[4] = 0;
  str_revs[9] = 0;
  if (last_mode == rev_display_mode)
    snprintf(str, sizeof(str), "%s A %s", str_curr, str_revs);
  else
    snprintf(str, sizeof(str), "%s A %s", str_curr,
             ((rev_display_mode == DISPLAY_LIFETIME) ? " LIFETIME" :
              ((rev_display_mode == DISPLAY_INCREMENTAL) ? "INCREMENT" : "")));

  // Instead of displaying revs, display some debug info:
  //snprintf(str, sizeof(str), "%6d %6d", adc_sample_rate, adc_val);
  //snprintf(str, sizeof(str), "%6d", adc_rms);

  str[16] = 0;
  lcd.setCursor(0, 1);
  lcd.print(str);


  // if new errors, flash an error message
  if (errors != last_errors) {
    lcd.setCursor(0, 0);
    lcd.print("Error   ");
  }

  last_errors = errors;
  last_mode = rev_display_mode;
}

// Update the RPM calculation every ~500 msec (while motor is running)
// Return 0 if new RPM value available, -1 otherwise.
// If the spindle has moved at all, set count_changed = TRUE.
// RPM > 0 indicates forward
// RPM < 0 indicates reverse
#if 0
int update_rpm(bool *count_changed)
{
  static uint32_t start_time, end_time;           // in microseconds
  static int32_t start_count, end_count;
  uint32_t curr_time; //, difftime;

  // Get delta T and delta count
  curr_time = micros();
  noInterrupts();
  end_count = hall_count;
  end_time = hall_count_time;
  interrupts();

  if (end_count == start_count)
    *count_changed = false;
  else
    *count_changed = true;

  // FIXME - we want to update ~500msec while motor is not running also...
  // if > 500 msec since last hall_count_time, then do it anyway.

  // If > 500 msec since last update, do it now
  //difftime = end_time - start_time;
  //if (difftime >= 500000) {

  // Handle the stall case where hall_count_time has not changed for > 500msec
  // We need an 'last_update_time' which is either based on the hall_count_time or
  // normal time.

  // Else case where motor is running
  if ((end_time - start_time) >= 500000) {
    rpm = hall_count_to_revs(end_count - start_count) / (end_time - start_time) * 1e6 * 60.0;
    start_time = end_time;
    start_count = end_count;
    return 0;
  }
  return -1;
}
#else
void update_rpm(void)
{
  //static uint32_t start_time, end_time;           // in microseconds
  //static int32_t start_count, end_count;
  uint32_t t;
  int32_t count;
  static uint32_t last_t;

  // Get delta T and delta count
  noInterrupts();
  //end_count = hall_count;
  //end_time = hall_count_time;
  count = hall_count;
  t = hall_count_time;
  interrupts();

  // Avoid divide by zero if the motor stopped.
  //if (end_time != start_time) {
  if (t != rpm_update_time) {
    //rpm = hall_count_to_revs(end_count - start_count) / (end_time - start_time) * 1e6 * 60.0;
    rpm = hall_count_to_revs(count - rpm_update_hall_count) / (t - rpm_update_time) * 1e6 * 60.0;
    //start_time = end_time;
    //start_count = end_count;
    rpm_update_time = t;
    rpm_update_hall_count = count;
  }
  // Also handle the case when the motor stops spinning
  else {
    rpm = 0;
  }
}
#endif


// Debounce the button and return:
// PRESSED - recognized immediately
// NOT_PRESSED - recognized after released for > debounce time
// SHORT_PRESS - upon release (after debounce), when held down briefly.
// LONG_PRESS - when held for longer than LONG_PRESS_TIME_MSEC. One shot, then transition to PRESSED state.
//
// SHORT_PRESS state is a one-shot. Next call returns NOT_PRESSED.
// LONG_PRESS state is a one-shot. Next call returns PRESSED.
//
// buttons should be array of size 2.

#define DEBOUNCE_TIME_MSEC        20
#define LONG_PRESS_TIME_MSEC      2500

// States used for debouncing and reporting button status
#define NOT_PRESSED               0
#define PRESSED                   1
#define LONG_PRESS                2
#define SHORT_PRESS               3
#define DEBOUNCE                  4     // internal state only
#define LONG_PRESSED              5     // internal state only
#define LONG_DEBOUNCE             6     // internal state only
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
void loop()
{
  static uint8_t led;
  static uint32_t lcd_update_time;
  static int32_t last_hall_count;
  int32_t count;
  float rms_volt;
  uint8_t buttons[2];
  int ret;
  uint16_t tmsec;

  // We want to run this loop fast.  This helps with button debouncing and possibly other things.
  tmsec = millis();

  digitalWrite(LED_BUILTIN, led);
  led = led ^ 1;

  // Handle the button. Short press means switch between incremental and absolute (lifetime).
  // Long press means zero incremental rev count.
  // Maybe also meanings for holding button at boot (and also for long hold > 10 seconds - factory default?)

  read_buttons(buttons);
  if (buttons[0] == LONG_PRESS) {
    // Clear rev counter
    noInterrupts();               // critical section - updated in ISR
    hall_count = 0;
    interrupts();
    lcd_update_time = 0;          // force immediate update
  }
  else if (buttons[0] == SHORT_PRESS) {
    // Toggle between incremental and absolute modes
    rev_display_mode ^= 1;
    digitalWrite(LED_GREEN, !digitalRead(LED_GREEN));
  }

  // If the spindle moved, update the FRAM.  FRAM write are essentially limitless, so this should be
  // safe. By writing FRAM often we minimize missed counts if power cuts unexpectedly.
  noInterrupts();
  count = hall_count;
  interrupts();
  if (count != last_hall_count) {
    // FRAM write takes about 3 msec @ 100KHz.
    store_fram();
    last_hall_count = count;
  }

  // Periodically compute the RPM and AC current, and update the LCD
  if ((tmsec - lcd_update_time) >= LCD_UPDATE_TIME_MSEC) {

    update_rpm();

    // Current sense transformer RMS voltage
    // Vrms = ADC_DN / 512 / Gain * 2.56
    rms_volt = (float)adc_rms / 512 * 2.56;

    // Calculate motor current.  Sensor is slightly nonlinear.
    // Irms = coil Vrms * 10.31 at Irms = 1A
    // Irms = coil Vrms * 10.0 at Irms = 10A
    motor_curr = rms_volt * (10.0 + (1.0 - rms_volt) * 0.333);

    update_lcd();
    lcd_update_time = tmsec;

    digitalWrite(LED_RED, !digitalRead(LED_RED));
  }

  // Loop delay
  delay(10);
}

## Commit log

2018-02-18 Initial import of the Arduino code.
2018-02-18 Initial import of the PCB files.
    [BOM-MOTOR_MONITOR_REV_A.csv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]
2018-02-18 Add updated BOM.
    [BOM-MOTOR_MONITOR_REV_A_Full.csv]
2018-02-18 Updated with preferred latching connector
    [BOM-MOTOR_MONITOR_REV_A_Full.csv]
2018-02-18 Redlined schematic
2018-02-19 Slower LCD update rate. Fix RPM startup bug. Bump version.
    [arduino_bldc_motor_monitor_rev_a.ino]
